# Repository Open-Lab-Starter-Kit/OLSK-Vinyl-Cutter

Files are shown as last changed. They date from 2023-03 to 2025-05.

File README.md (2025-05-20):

<div align="center"><h1 style=align="center">OLSK Vinyl Cutter V3</h1></div>

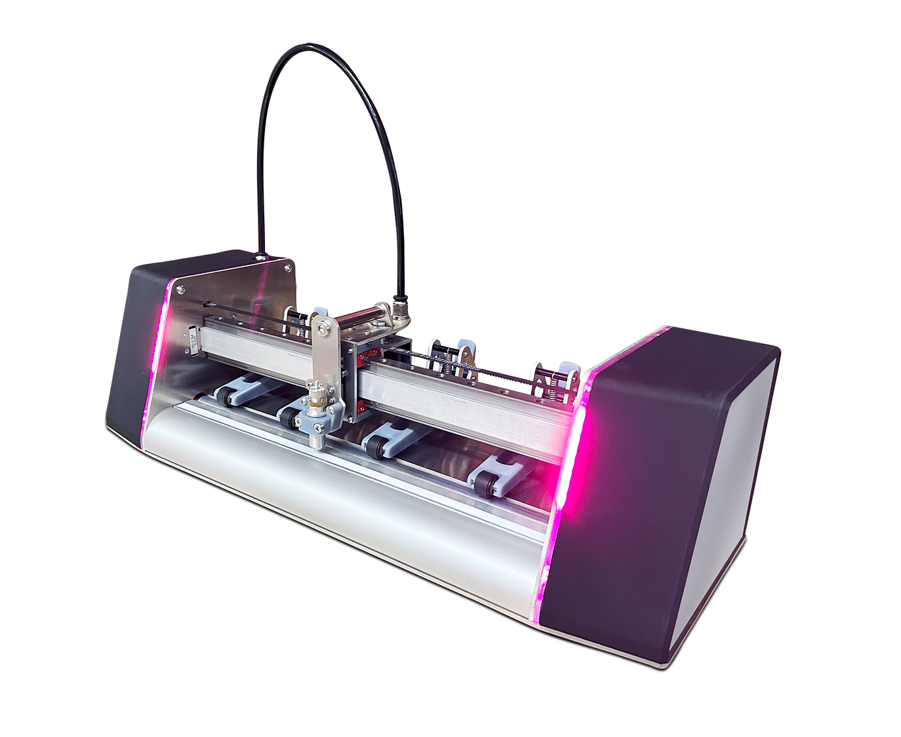
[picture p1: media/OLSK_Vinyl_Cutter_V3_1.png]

<div align="center"><i>Open Source Vinyl Cutter - Open Lab Starter Kit</i></div>

<br>

The Assembly Manual
--

All OLSK machines are open source and have an assembly manual, the BOM and necessary files available in this repository for replication. The assembly manual is an interactive 3D guide though each step and contains a list of parts, tools and instruction remarks, which follows a logical order to provide a smooth assembly.

- **[Assembly Manual](https://open-lab-starter-kit.github.io/OLSK-Vinyl-Cutter/)**

<br>
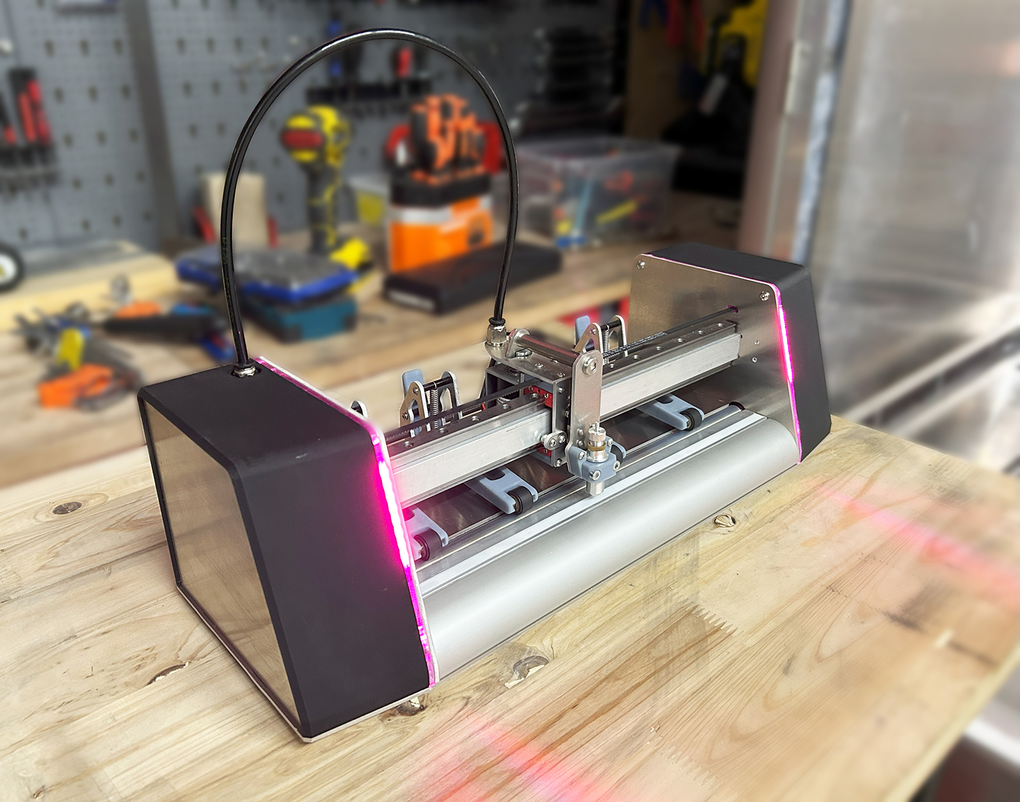
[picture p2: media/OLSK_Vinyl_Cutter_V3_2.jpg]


<br>

Specifications V3
--

- cutting area: A3
- frame: CNC milled 3mm aluminum
- motion: Belt and linear guide
- drivers: TMC drivers with 1/256 microstepping interpolation
- decoupled motors
- continuous duty solenoid
- pinch rollers: 4 units with bistable locking mechanism
- indicator lights
- software: OLOS
- job preview
- file manager

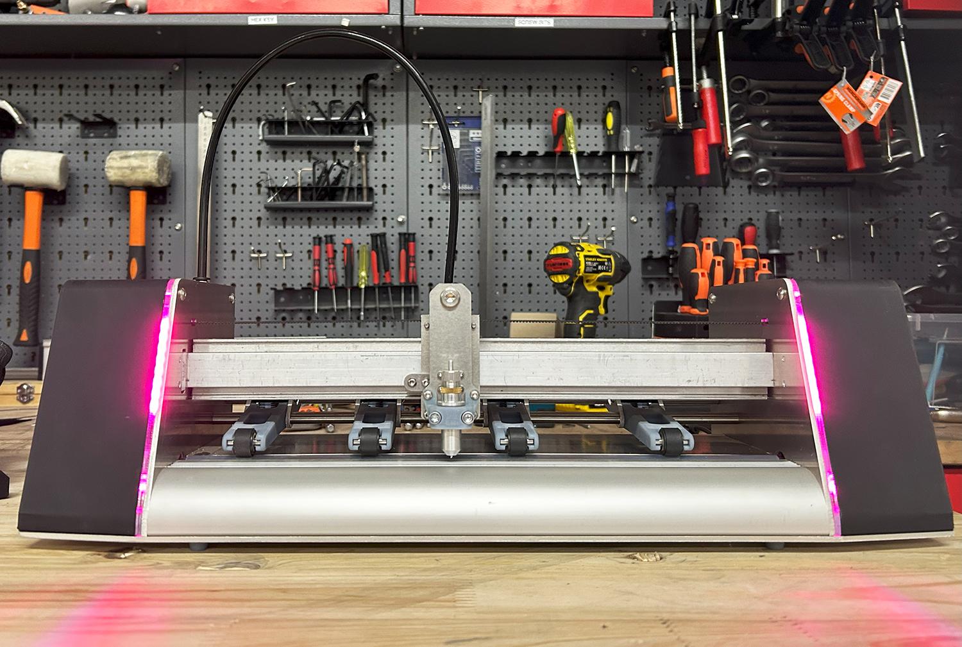
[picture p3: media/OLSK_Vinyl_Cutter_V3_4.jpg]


Files
--

- **[CAD](cad)**
- **[Firmware](firmware)**
- **[Settings](settings)**
- **[BOM](OLSK_Vinyl_Cutter_V3-BOM.xlsx)**
- **[Wiring Schematic](OLSK_Vinyl_Cutter_V3_WiringSchematic.pdf)**

Author
--


<br>

OLSK Vinyl Cutter has been designed and built by **[InMachines Ingrassia GmbH](https://www.inmachines.net/)**.

Machine design:
- **[Wilhelm Schütze](http://fabacademy.org/archives/2015/sa/students/schutze.wilhelm/index.html)**

The machine is part of the **[Open Lab Starter Kit (OLSK)](https://www.inmachines.net/open-lab-starter-kit)** group of open source digital fabrication machines.

OLSK is developed by **[InMachines Ingrassia GmbH](https://www.inmachines.net/)** for the **[Dtec project](https://dtecbw.de/home/forschung/hsu/projekt-fabcity)** at **[Fab City Hamburg](https://www.fabcity.hamburg/en/)**.

OLSK Partners:
<br><br>


Contact
--

- daniele@inmachines.net
- [https://www.inmachines.net/](https://www.inmachines.net/)

License
--

See the LICENSES folder and the SPDX metadata for more details on other files.
The project is [REUSE](https://reuse.software/) compliant

Hardware design, CAD and PCB files, BOM, settings and other technical or design files are released under the following license:

- CERN Open Hardware Licence Version 2 Weakly Reciprocal - **[CERN-OHL-W](LICENSE_CERN_OHL_W_V2.txt)**

Assembly manual, pictures, videos, presentations, description text and other type of media are released under the following license:

- Creative-Commons-Attribution-ShareAlike 4.0 International - **[CC BY-SA 4.0](LICENSE_CC_BY_SA_4.0.txt)**

Copyright
--

- Daniele Ingrassia, InMachines Ingrassia GmbH

- Tobias Redlich, Helmut-Schmidt-Universität/Universität der Bundeswehr Hamburg

Previous version
--

The previous versions of OLSK machines will always be available.

**[OLSK Vinyl Cutter V2 Repository](OLSK_Vinyl_Cutter_V2)**
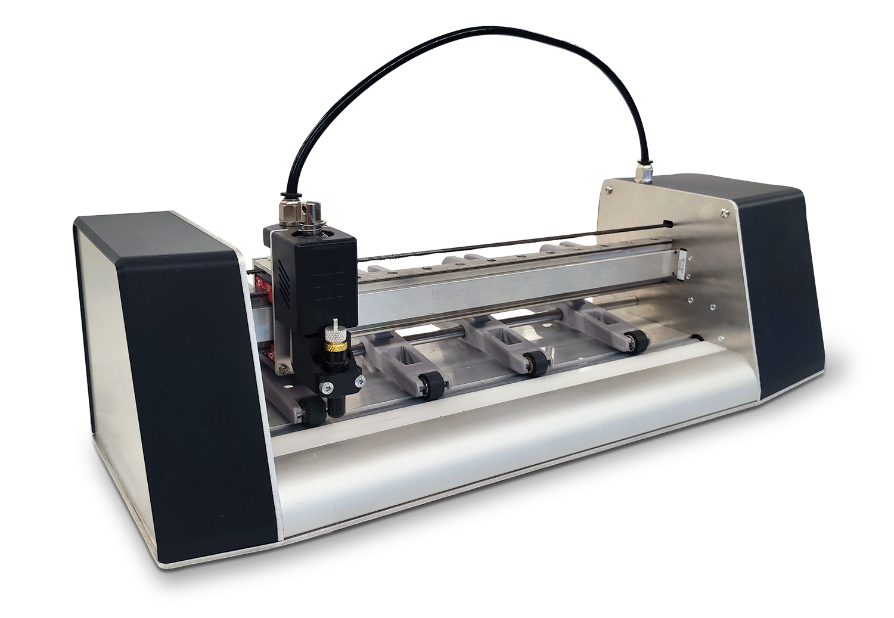
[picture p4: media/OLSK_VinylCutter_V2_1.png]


**[OLSK Vinyl Cutter V1 Repository](OLSK_Vinyl_Cutter_V1)**
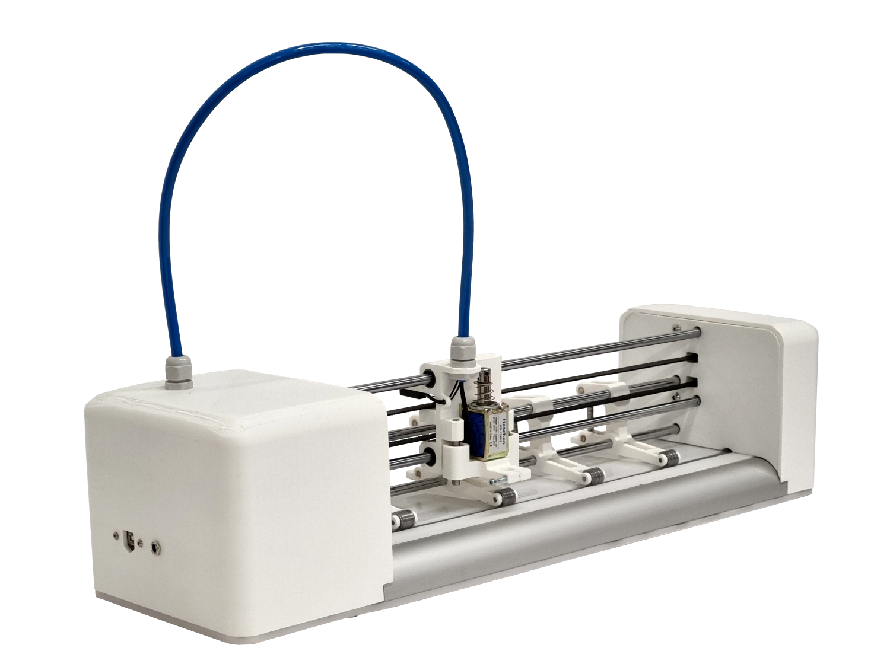
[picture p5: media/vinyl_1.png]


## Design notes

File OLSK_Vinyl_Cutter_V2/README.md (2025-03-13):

<div align="center"><h1 style=align="center">OLSK Vinyl Cutter V2</h1></div>


<div align="center"><i>Open Source Vinyl Cutter - Open Lab Starter Kit</i></div>

<br>

Specifications V2
--



- cutting area: 300mm
- frame: CNC milled 3mm aluminum 
- motion: Belt and linear guide
- drivers: TMC drivers with 1/256 microstepping interpolation

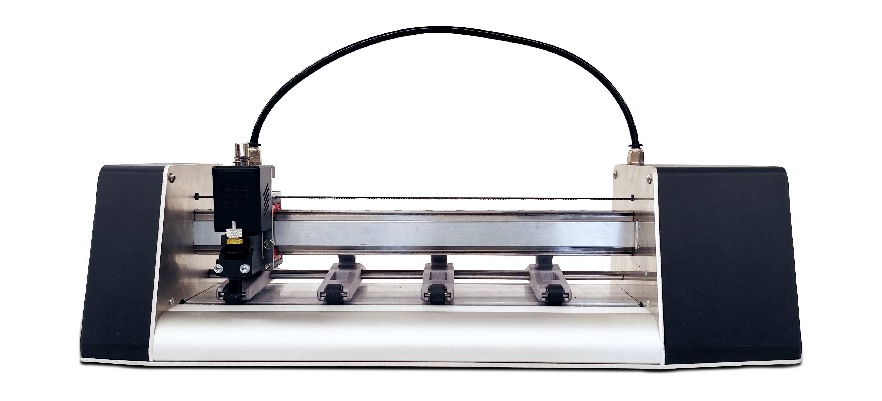
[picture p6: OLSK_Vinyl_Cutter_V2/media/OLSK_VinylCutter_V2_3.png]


Files
--

- **[CAD](cad)**
- **[Firmware](firmware)**
- **[Assembly Steps](OLSK_Vinyl_Cutter_V2_AssemblySteps.pdf)**
- **[Wiring Schematic](OLSK_Vinyl_Cutter_V2_WiringSchematic.pdf)**

Author
--


<br>

OLSK Vinyl Cutter has been designed and built by **[InMachines Ingrassia GmbH](https://www.inmachines.net/)**.

Machine design:
- **[Wilhelm Schütze](http://fabacademy.org/archives/2015/sa/students/schutze.wilhelm/index.html)**

The machine is part of the **[Open Lab Starter Kit (OLSK)](https://www.inmachines.net/open-lab-starter-kit)** group of open source digital fabrication machines.

OLSK is developed by **[InMachines Ingrassia GmbH](https://www.inmachines.net/)** for the **[Dtec project](https://dtecbw.de/home/forschung/hsu/projekt-fabcity)** at **[Fab City Hamburg](https://www.fabcity.hamburg/en/)**.

OLSK Partners:
<br><br>


Contact
--

- daniele@inmachines.net
- [https://www.inmachines.net/](https://www.inmachines.net/)

License
--

Hardware design, CAD and PCB files, BOM, settings and other technical or design files are released under the following license:

- CERN Open Hardware Licence Version 2 Weakly Reciprocal - **[CERN-OHL-W](LICENSE_CERN_OHL_W_V2.txt)**

Assembly manual, pictures, videos, presentations, description text and other type of media are released under the following license:

- Creative-Commons-Attribution-ShareAlike 4.0 International - **[CC BY-SA 4.0](LICENSE_CC_BY_SA_4.0.txt)**

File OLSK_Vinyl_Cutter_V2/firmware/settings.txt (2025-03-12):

$0 = 10.0    (Step pulse time, microseconds)
$1 = 25    (Step idle delay, milliseconds)
$2 = 0    (Step pulse invert, mask)
$3 = 0    (Step direction invert, mask)
$4 = 7    (Invert step enable pin, boolean)
$5 = 6    (Invert limit pins, boolean)
$6 = 1    (Invert probe pin, boolean)
$9 = 1   
$10 = 511    (Status report options, mask)
$11 = 0.010    (Junction deviation, millimeters)
$12 = 0.002    (Arc tolerance, millimeters)
$13 = 0    (Report in inches, boolean)
$14 = 70   
$15 = 0   
$16 = 0   
$17 = 0   
$18 = 0   
$19 = 0   
$20 = 1    (Soft limits enable, boolean)
$21 = 1    (Hard limits enable, boolean)
$22 = 1    (Homing cycle enable, boolean)
$23 = 0    (Homing direction invert, mask)
$24 = 2000.0    (Homing locate feed rate, mm/min)
$25 = 2000.0    (Homing search seek rate, mm/min)
$26 = 250    (Homing switch debounce delay, milliseconds)
$27 = 3.000    (Homing switch pull-off distance, millimeters)
$28 = 0.100   
$29 = 0.0   
$30 = 1000.000    (Maximum spindle speed, RPM)
$31 = 0.000    (Minimum spindle speed, RPM)
$32 = 1    (Laser-mode enable, boolean)
$33 = 5000.0   
$34 = 0.0   
$35 = 0.0   
$36 = 100.0   
$37 = 0   
$39 = 1   
$40 = 0   
$43 = 1   
$44 = 4   
$45 = 3   
$46 = 0   
$62 = 0   
$63 = 3   
$64 = 0   
$65 = 0   
$100 = 46.00000    (X-axis travel resolution, step/mm)
$101 = 94.60000    (Y-axis travel resolution, step/mm)
$102 = 1.00000    (Z-axis travel resolution, step/mm)
$110 = 3000.000    (X-axis maximum rate, mm/min)
$111 = 3000.000    (Y-axis maximum rate, mm/min)
$112 = 500.000    (Z-axis maximum rate, mm/min)
$120 = 250.000    (X-axis acceleration, mm/sec^2)
$121 = 250.000    (Y-axis acceleration, mm/sec^2)
$122 = 250.000    (Z-axis acceleration, mm/sec^2)
$130 = 300.000    (X-axis maximum travel, millimeters)
$131 = 2000.000    (Y-axis maximum travel, millimeters)
$132 = 1.000    (Z-axis maximum travel, millimeters)
$341 = 0   
$342 = 30.0   
$343 = 25.0   
$344 = 200.0   
$345 = 200.0   
$346 = 1   
$370 = 8   
$372 = 0   
$384 = 0   
$398 = 100   
$481 = 0   
$484 = 1   
$486 = 0

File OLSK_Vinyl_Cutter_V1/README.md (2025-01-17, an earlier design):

<div align="center"><h1 style=align="center">OLSK Vinyl Cutter V1</h1></div>


<div align="center"><i>Open Source Vinyl Cutter - Open Lab Starter Kit</i></div>

<br>

Specifications V1
--

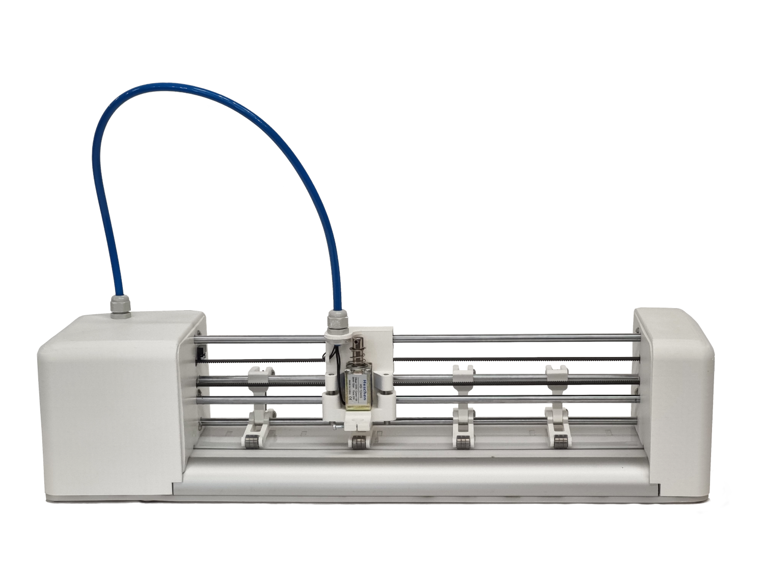
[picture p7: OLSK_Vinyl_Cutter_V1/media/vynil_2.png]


- cutting area: 350mm
- frame: CNC milled 3mm aluminum 
- motion: GT2 10mm belt
- guides: 8mm linear shafts
- motors: stepper NEMA 17

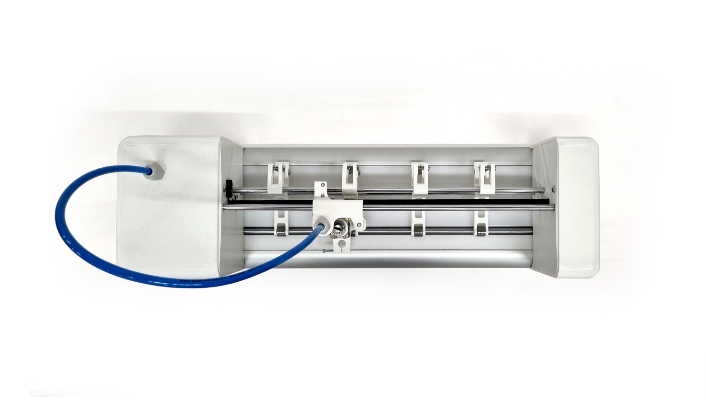
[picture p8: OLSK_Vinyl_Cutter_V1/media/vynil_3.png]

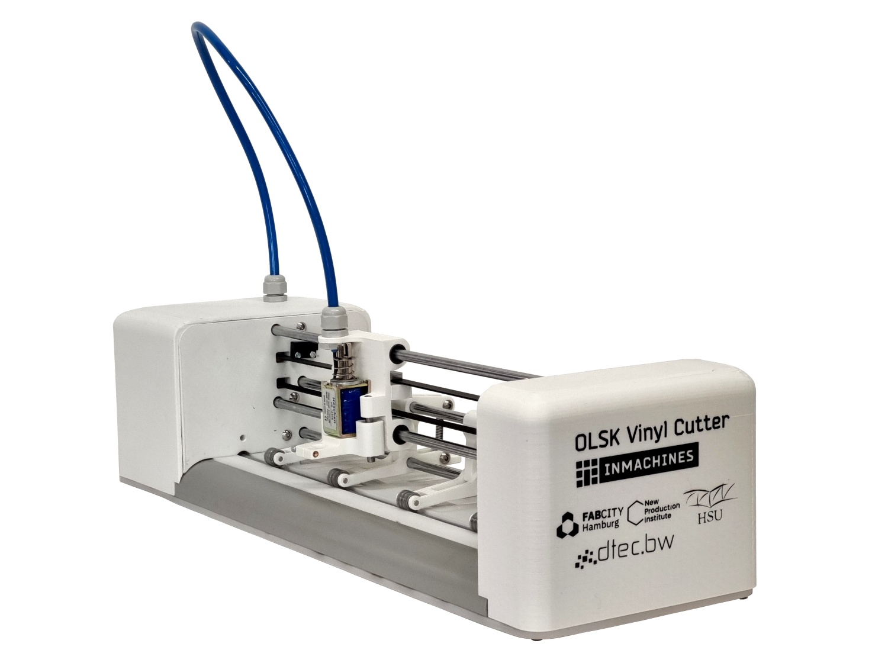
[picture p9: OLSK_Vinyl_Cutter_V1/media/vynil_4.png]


Files
--

- **[BOM](BOM)**
- **[CAD](cad)**
- **[Settings](settings)**
- **[Assembly Workbook](OLSK_VinylCutter_V1_Workbook.pdf)**
- **[Wiring Schematic](OLSK_Vinyl_Cutter_V1_WiringSchematic.pdf)**

Author
--


<br>

OLSK Vinyl Cutter has been designed and built by **[InMachines Ingrassia GmbH](https://www.inmachines.net/)**.

Machine design:
- **[Daniele Ingrassia](https://www.linkedin.com/in/danieleingrassia/)**

The machine is part of the **[Open Lab Starter Kit (OLSK)](https://www.inmachines.net/open-lab-starter-kit)** group of open source digital fabrication machines.

OLSK is developed by **[InMachines Ingrassia GmbH](https://www.inmachines.net/)** for the **[Dtec project](https://dtecbw.de/home/forschung/hsu/projekt-fabcity)** at **[Fab City Hamburg](https://www.fabcity.hamburg/en/)**.

OLSK Partners:
<br><br>


Contact
--

- daniele@inmachines.net
- [https://www.inmachines.net/](https://www.inmachines.net/)

License
--

Hardware design, CAD and PCB files, BOM, settings and other technical or design files are released under the following license:

- CERN Open Hardware Licence Version 2 Weakly Reciprocal - **[CERN-OHL-W](LICENSE_CERN_OHL_W_V2.txt)**

Assembly manual, pictures, videos, presentations, description text and other type of media are released under the following license:

- Creative-Commons-Attribution-ShareAlike 4.0 International - **[CC BY-SA 4.0](LICENSE_CC_BY_SA_4.0.txt)**

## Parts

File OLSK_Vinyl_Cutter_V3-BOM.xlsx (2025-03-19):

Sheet: sheet1
Part Name | Quantity
Alu Profile 30x30 Nut 8 - R3030 | 2
Tool Plate (3mm alu laser cutted/milled) | 1
Alluminium pulley GT2 20T 6mm - 5mm bore | 1
Pinch roller side plate (3mm alu laser cutted/milled | 8
OLSK vinyl cutter PCB | 1
DC switch - KCD11 | 1
Linear Block - MGN7CZFC | 1
Y closed decoupling timing belt GT2 4mm 132mm | 1
Pinch roller A part (3D printed) | 4
Spring 1x6x30mm | 4
Pinch roller wheel 14mm 4mm bore | 4
Y motor bracket (3D printed) | 1
X motor bracket (3D printed) | 1
Pinch roller B part (3D printed) | 4
Head front plate (3mm alu laser cutted/milled) | 1
Aluminium spacer M3 12mm | 8
Linear guide - MGNR12 345mm | 2
Left main bracket (3D printed) | 1
Aluminium spacer M3 25mm | 8
Light diffuser right (3mm Laser cut acrylic) | 1
Led PCB strip - 8 bit - WS2812-8 | 2
Right Plate (3mm alu laser cutted/milled) | 1
Top cover bracket right (3D printed) | 1
Shaft 12mm x 450mm h6, stainless steel X46Cr13 | 1
X beam - Alu beam 20x20x3x380mm (drilled) | 1
Sensor PS-3150 | 1
X motor bracket (3D printed) | 1
Shaft 4x20mm | 8
Linear block - MGN12C | 2
Alluminium pulley GT2 36T 6mm - 12mm bore | 1
Head top plate (3mm alu laser cutted/milled) | 1
Timing belt GT2 6mm 1M | 1
Bearing holder (3D printed) | 1
Left side plate (3mm alu laser cutted/milled) | 1
Feet (3D printed) | 4
Left side cover (3D printed) | 1
USB type B panel mount - 907 | 1
Solenoid - B22-254-M-36 | 1
Right side plate (3mm alu laser cutted/milled) | 1
Deep groove ball bearing 6801 | 2
Linear guide - MGNR7R55CM | 1
Light diffuser left (3mm Laser cut acrylic) | 1
Head back plate (3mm alu laser cutted/milled) | 1
Cutting beam left bracket (3D printed) | 1
Tool holder back (3D printed) | 1
Stepper motor driver - TMC2130-V3.0 | 2
Stepper motor 17HM19-2004S | 1
Led holder Left (3D printed) | 1
Head top bracket (3D printed) | 1
Neodymium magnet- round 8mmx3mm w/ countersink hole for M3 bolt | 1
Silicon Pipe 12x14mm 350mm | 1
Led Holder Right (3D printed) | 1
Bottom plate cover (3mm Laser cut acrylic) | 1
Solenoid round spacer 10x58.5mm | 1
DC barrel plug - panel mount 5.5 x 2.1mm | 1
Orange Pie - OPiZ2W | 1
Right side cover (3D printed) | 1
Tool holder front (3D printed) | 1
Shaft 8mm x 350mm h6, stainless steel X46Cr13 (ends drilled and tapped M4) | 2
Left plate (3mm alu laser cutted/milled) | 1
Alluminium idler pulley GT2 36T 6mm - 5mm bore | 1
Cutting beam right bracket (3D printed) | 1
Head bottom bracket (3D printed) | 1
Teflon strip, 0.8x8x350mm | 1
Top plate stopper (3mm alu laser cutted/milled) | 1
Push-To-Connect fitting 1-8 MNPT x 6mm | 2
Alluminium pulley GT2 36T 6mm - 5mm bore | 1
Stepper motor 17HS13-0404S1 | 1
Top cover bracket left (3D printed) | 1
Bottom plate (3mm alu laser cutted/milled) | 1
Blade Holder | 1
Solenoid connecting plate (3mm alu laser cutted/milled) | 1
Cutting beam - Alu beam 20x20x3x380mm (milled) | 1
Top cover (3mm alu laser cutted/milled) | 1
Fasteners
Hexagon Socket Button Head Screw ISO 7380-1 - M3 x 10 | 4
Hexagon Socket Button Head Screw ISO 7380-1 - M3 x 12 | 6
Hexagon Socket Button Head Screw ISO 7380-1 - M3 x 16 | 4
Hexagon Socket Button Head Screw ISO 7380-1 - M3 x 20 | 4
Hexagon Socket Button Head Screw ISO 7380-1 - M3 x 35 | 4
Hexagon Socket Button Head Screw ISO 7380-1 - M3 x 6 | 30
Hexagon Socket Button Head Screw ISO 7380-1 - M3 x 8 | 6
Hexagon Socket Button Head Screw ISO 7380-1 - M4 x 20 | 2
Hexagon Socket Button Head Screw ISO 7380-1 - M4 x 8 | 6
Hexagon Socket Button Head Screw ISO 7380-1 - M8 x 65 | 1
Hexagon Socket Head Cap Screw DIN 912 - M2 x 5 | 4
Hexagon Socket Head Cap Screw DIN 912 - M2 x 6 | 4
Hexagon Socket Head Cap Screw DIN 912 - M2.5 x 6 | 4
Hexagon Socket Head Cap Screw DIN 912 - M3 x 10 | 4
Hexagon Socket Head Cap Screw DIN 912 - M3 x 12 | 16
Hexagon Socket Head Cap Screw DIN 912 - M3 x 4 | 2
Hexagon Socket Head Cap Screw DIN 912 - M3 x 6 | 18
Hexagon Socket Head Cap Screw DIN 912 - M4 x 10 | 6
Hexagon Socket Head Cap Screw DIN 912 - M4 x 12 | 10
Hexagon Socket Head Cap Screw DIN 912 - M4 x 20 | 6
Hexagon Socket Head Cap Screw DIN 912 - M4 x 8 | 3
Hexagon Socket Head Cap Screw DIN 912 - M5 x 10 | 2
Hexagon Socket Head Cap Screw DIN 912 - M5 x 8 | 1
Hexagon Socket Head Cap Screw DIN 912 - M8 x 12 | 4
Hexagon Socket Head Shoulder Screw ISO 7379 - 5 x 25 | 1
Hexagon socket countersunk head cap screw DIN 7991 M3 x 6 | 1
Set Screw DIN 913 - M3 x 5 | 5
Set Screw DIN 913 - M3 x 8 | 1
Hexagon Nut DIN 985 - M4 | 3
Hexagon Thin Nut DIN 439-2 - M8 | 1
T slot nut 8 m3 | 6
T slot nut_8 m5_ | 1
Nylon M3 nut | 12
Threaded insert M4 6x6mm | 4
Treaded insert M3 5x6mm | 4
Washer DIN 125-1 M4 | 2
Spacer PCB M3 10mm | 4

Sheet: Hoja 1
1.69.4 | Hexagon Socket Button Head Screw ISO 7380-1 - M3 x 10 | 4
1.69.8 | Hexagon Socket Button Head Screw ISO 7380-1 - M3 x 12 | 6
1.69.13 | Hexagon Socket Button Head Screw ISO 7380-1 - M3 x 16 | 4
1.69.47 | Hexagon Socket Button Head Screw ISO 7380-1 - M3 x 20 | 4
1.69.17 | Hexagon Socket Button Head Screw ISO 7380-1 - M3 x 35 | 4
1.69.21 | Hexagon Socket Button Head Screw ISO 7380-1 - M3 x 6 | 30
1.69.32 | Hexagon Socket Button Head Screw ISO 7380-1 - M3 x 8 | 6
1.69.38 | Hexagon Socket Button Head Screw ISO 7380-1 - M4 x 20 | 2
1.69.40 | Hexagon Socket Button Head Screw ISO 7380-1 - M4 x 8 | 6
1.69.46 | Hexagon Socket Button Head Screw ISO 7380-1 - M8 x 65 | 1
1.69.49 | Hexagon Socket Head Cap Screw DIN 912 - M2 x 5 | 4
1.69.50 | Hexagon Socket Head Cap Screw DIN 912 - M2 x 6 | 4
1.69.51 | Hexagon Socket Head Cap Screw DIN 912 - M2.5 x 6 | 4
1.69.55 | Hexagon Socket Head Cap Screw DIN 912 - M3 x 10 | 4
1.69.59 | Hexagon Socket Head Cap Screw DIN 912 - M3 x 12 | 16
1.69.75 | Hexagon Socket Head Cap Screw DIN 912 - M3 x 4 | 2
1.69.76 | Hexagon Socket Head Cap Screw DIN 912 - M3 x 6 | 18
1.69.94 | Hexagon Socket Head Cap Screw DIN 912 - M4 x 10 | 6
1.69.100 | Hexagon Socket Head Cap Screw DIN 912 - M4 x 12 | 10
1.69.110 | Hexagon Socket Head Cap Screw DIN 912 - M4 x 20 | 6
1.69.115 | Hexagon Socket Head Cap Screw DIN 912 - M4 x 8 | 3
1.69.118 | Hexagon Socket Head Cap Screw DIN 912 - M5 x 10 | 2
1.69.120 | Hexagon Socket Head Cap Screw DIN 912 - M5 x 8 | 1
1.69.121 | Hexagon Socket Head Cap Screw DIN 912 - M8 x 12 | 4
1.69.125 | Hexagon Socket Head Shoulder Screw ISO 7379 - 5 x 25 | 1
1.69.129 | Hexagon socket countersunk head cap screw DIN 7991 M3 x 6 | 1
1.69.130 | Set Screw DIN 913 - M3 x 5 | 5
1.69.136 | Set Screw DIN 913 - M3 x 8 | 1
1.69.2 | Hexagon Nut DIN 985 - M4 | 3
1.69.126 | Hexagon Thin Nut DIN 439-2 - M8 | 1
1.69.137 | T slot nut 8 m3 | 6
1.69.138 | T slot nut_8 m5_ | 1
1.69.128 | Nylon M3 nut | 12
1.69.127 | Threaded insert M4 6x6mm | 4
1.69.139 | Treaded insert M3 5x6mm | 4
1.69.140 | Washer DIN 125-1 M4 | 2
1.69.1 | Spacer PCB M3 10mm | 4

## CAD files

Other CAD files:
cad/OLSK-Vinyl-Cutter.f3z

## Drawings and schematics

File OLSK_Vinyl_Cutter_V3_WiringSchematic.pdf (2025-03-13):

# OLSK VINYL CUTTER V3

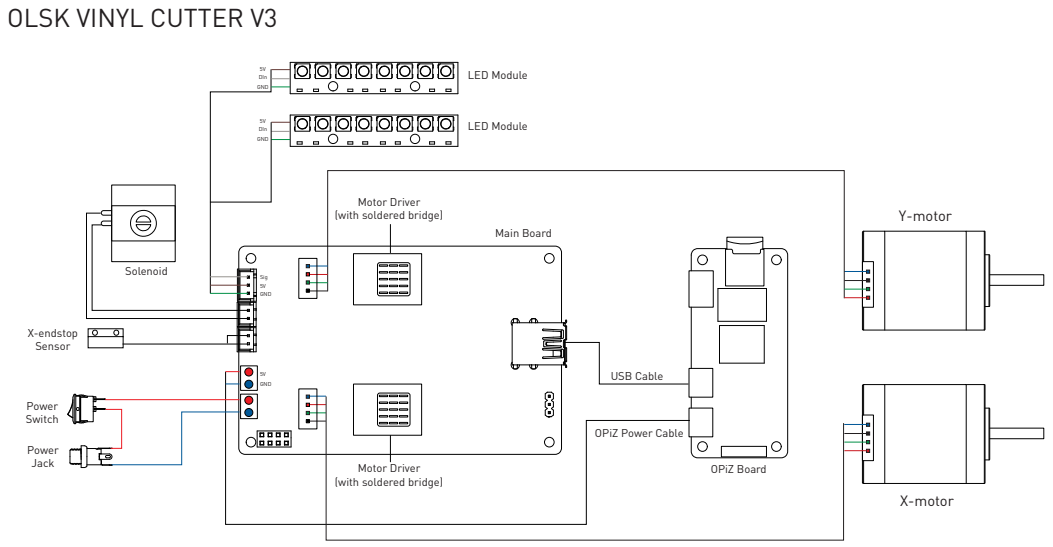
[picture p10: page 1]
X-endstop Sensor; Power Jack; Power Switch; Main Board; OPiZ Board; USB Cable; 5V DIn GND; Sig; GND; Solenoid; LED Module; X-motor; Y-motor

Motor Driver
(with soldered bridge)

OPiZ Power Cable

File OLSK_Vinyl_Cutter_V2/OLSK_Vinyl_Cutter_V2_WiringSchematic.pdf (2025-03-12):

# OLSK VINYL CUTTER V2

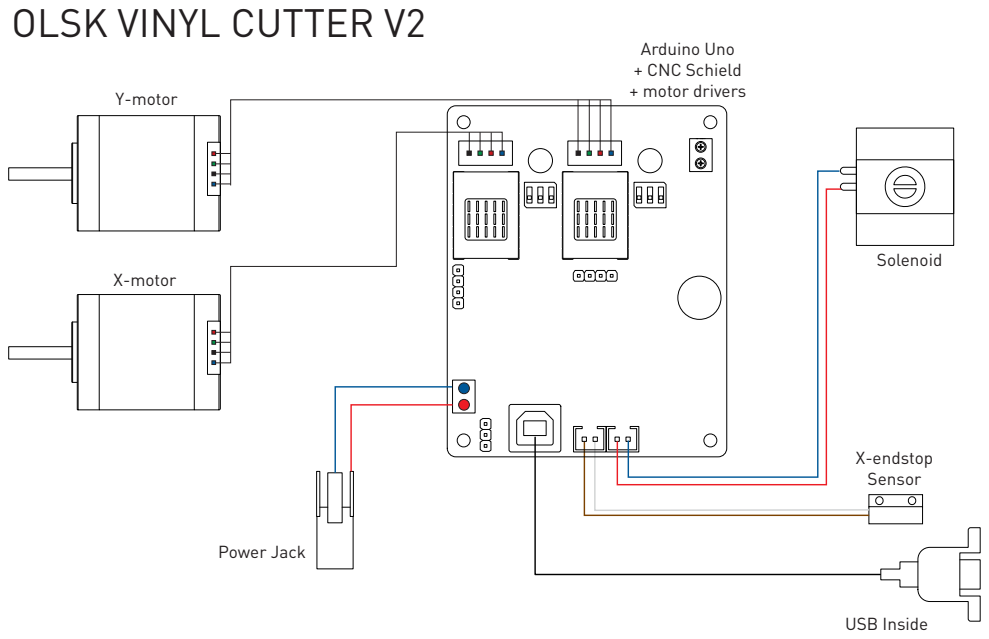
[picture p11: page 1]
X-endstop Sensor; X-motor; Y-motor; Power Jack; USB Inside; Arduino Uno + CNC Schield + motor drivers; Solenoid

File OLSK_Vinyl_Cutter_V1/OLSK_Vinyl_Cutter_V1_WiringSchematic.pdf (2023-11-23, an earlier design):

# OLSK VINYL CUTTER V1

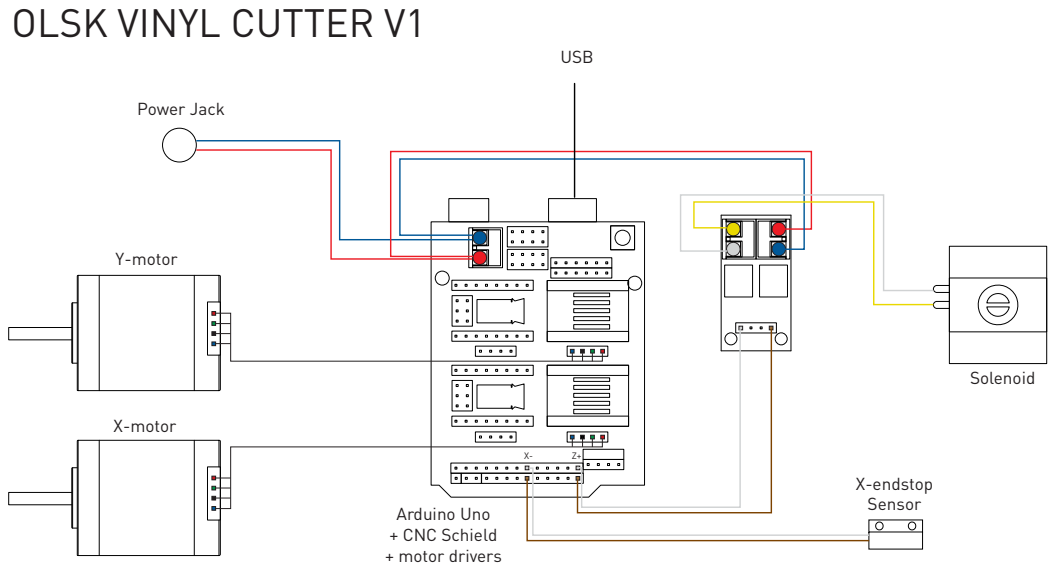
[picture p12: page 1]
X-endstop Sensor; X-motor; Y-motor; Power Jack; USB; Arduino Uno + CNC Schield + motor drivers; Solenoid

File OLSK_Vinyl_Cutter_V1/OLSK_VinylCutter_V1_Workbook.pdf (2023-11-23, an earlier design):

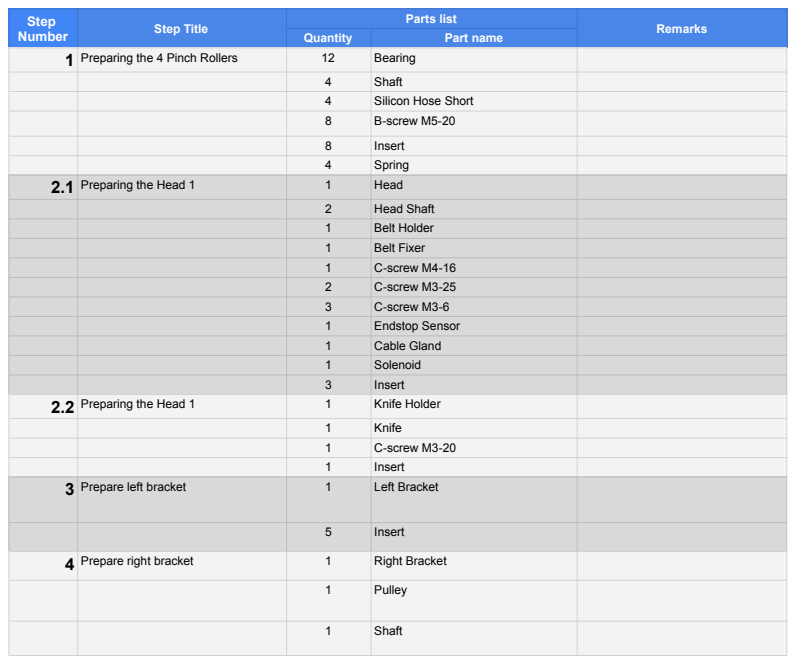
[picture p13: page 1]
Step; Number; Step Title; Parts list; Remarks; Quantity; Part name; 1 Preparing the 4 Pinch Rollers; Bearing; Shaft; Silicon Hose Short; B-screw M5-20; Insert; Spring; 2.1 Preparing the Head 1; Head; Head Shaft; Belt Holder; Belt Fixer; C-screw M4-16; C-screw M3-25; C-screw M3-6; Endstop Sensor; Cable Gland; Solenoid; 2.2 Preparing the Head 1; Knife Holder; Knife; C-screw M3-20; 3 Prepare left bracket; Left Bracket; 4 Prepare right bracket; Right Bracket; Pulley

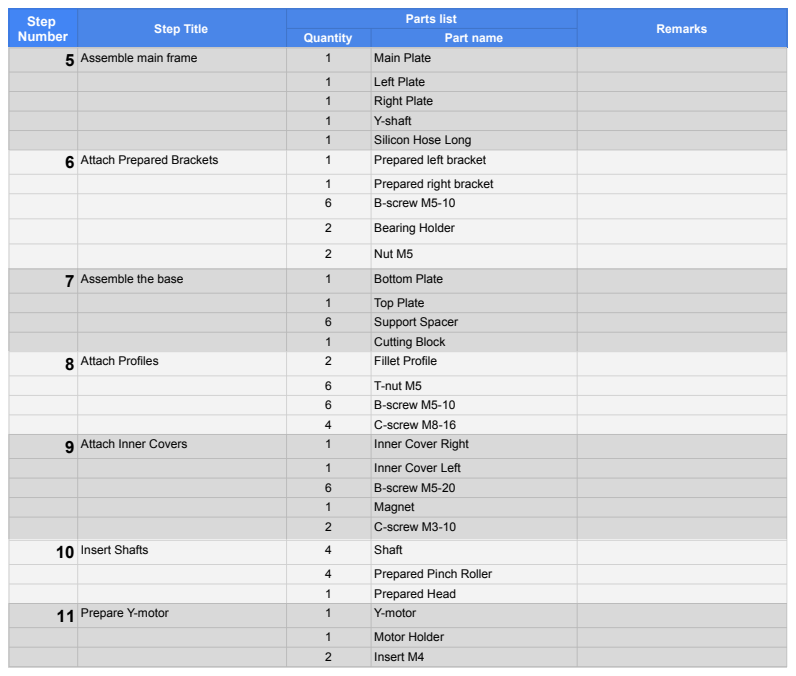
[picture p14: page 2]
5 Assemble main frame; Main Plate; Left Plate; Right Plate; Y-shaft; Silicon Hose Long; 6 Attach Prepared Brackets; Prepared left bracket; Prepared right bracket; B-screw M5-10; Bearing Holder; Nut M5; 7 Assemble the base; Bottom Plate; Top Plate; Support Spacer; Cutting Block; 8 Attach Profiles; Fillet Profile; T-nut M5; C-screw M8-16; 9 Attach Inner Covers; Inner Cover Right; Inner Cover Left; B-screw M5-20; Magnet; C-screw M3-10; 10 Insert Shafts; Shaft; Prepared Pinch Roller; Prepared Head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

Step Number | Step Title | Parts list | Remarks

Quantity | Part name

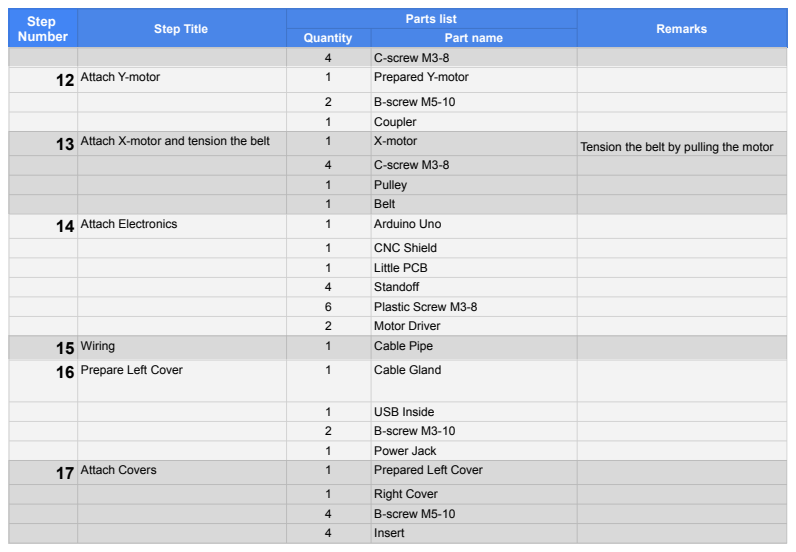
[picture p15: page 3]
C-screw M3-8; 12 Attach Y-motor; Prepared Y-motor; B-screw M5-10; Coupler; 13 Attach X-motor and tension the belt; X-motor; Tension the belt by pulling the motor; Pulley; Belt; 14 Attach Electronics; Arduino Uno; CNC Shield; Little PCB; Standoff; Plastic Screw M3-8; Motor Driver; 15 Wiring; Cable Pipe; 16 Prepare Left Cover; Cable Gland; USB Inside; B-screw M3-10; Power Jack; 17 Attach Covers; Prepared Left Cover; Right Cover; Insert

Step Number | Step Title | Parts list | Remarks

Quantity | Part name

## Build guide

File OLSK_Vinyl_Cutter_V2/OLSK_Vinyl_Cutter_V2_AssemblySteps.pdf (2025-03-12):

Step number | Step Instructions | Parts
1 | Assemble base | Base plate, fillet profiles, bottom cover and cutting rod
2 | Prepare x-axis | X-beam, linear shafts, head support
3 | Prepare 4 pinchrollers
4 | Prepare side panels | Bearing holders and sensor
5 | Install side panels fitting the x-axis, pinchrollers shaft and y-shaft inbetween | Prepared x-axis, pinchrollers, pinchrollers' shaft, y-shaft
6 | Install motors and tension the belts | Motors and belt
7 | Install electronics
8 | Install the head
9 | Wiring 1
10 | Prepare right side cover
11 | Wiring 2
12 | Install side covers
13 | Fix the knife

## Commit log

2023-04-17 Delete OLSK-Vinyl-Cutter.f3z
    updating the 3D design
    [OLSK-Vinyl-Cutter.f3z]
2023-04-17 added BOM files and updated 3D Deisgn
    [BOM OLSK Vinyl Cutter V1.ods, BOM OLSK Vinyl Cutter V1.xlsx]
2025-01-17 Assembly Manual fixes
2025-01-17 Assembly Mamual fixes
2025-03-12 Move V1 to folder
    [BOM OLSK Vinyl Cutter V1.ods, BOM OLSK Vinyl Cutter V1.xlsx]
2025-03-13 Update Assembly Manual
2025-03-19 Update V3
    [OLSK_Vinyl_Cutter_V3-BOM.xlsx]
